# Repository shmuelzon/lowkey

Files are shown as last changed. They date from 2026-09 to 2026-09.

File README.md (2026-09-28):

# LowKey

A battery-powered smart lock controller for a motorised deadbolt, built on the
Nordic **nRF54L15** with the nRF Connect SDK.

It speaks **Matter over Thread** and a **custom BLE GATT service at the same
time**, on one Bluetooth controller. The two are not alternatives selected at
build time - they run concurrently, each with its own advertising set and its
own Bluetooth identity, so the lock stays controllable over BLE when the Thread
mesh or the Matter controller is down, and its BLE bonds survive Matter
commissioning and Matter factory resets.

| On the bench | Installed in a door |
| --- | --- |
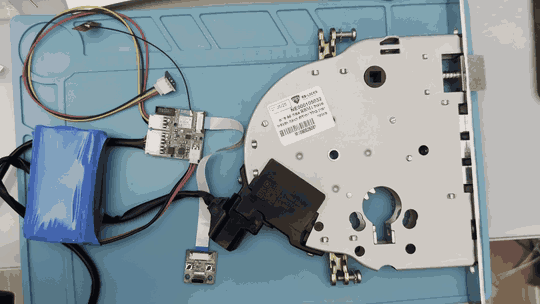
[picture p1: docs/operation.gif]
Locking and unlocking the RBM1 lock body, with the unassembled controller and UI boards on the bench
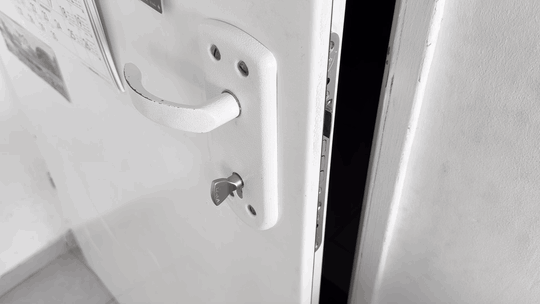
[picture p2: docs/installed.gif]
The installed lock throwing and retracting its bolts from the edge of a door
|  |  |

## Features

- **Three distinct actions**, matching what a mortise deadbolt can actually do:
  lock, unbolt (retract the bolt, spring latch still holds the door), and open
  (retract the bolt *and* hold the latch back so the door can be pushed).
  These map to the Matter `LockDoor`, `UnboltDoor` and `UnlockDoor` commands.
- **Position tracked from the bolt, not from the motor.** The lock body's two
  magnetic end-stop sensors are monitored continuously, so operating the lock
  with a physical key updates the reported state exactly like a remote command
  does.
- **Jam detection** - the motor stops and the lock reports jammed, with a Matter
  `DoorLockAlarm` event, if an end-stop is not reached in time.
- **Door position sensor**, reported as a Matter `DoorStateChange`.
- **Battery monitoring** with a MAX17205 ModelGauge m5 fuel gauge, plus charger
  connected/complete status.
- **Firmware update** over both Bluetooth SMP (MCUmgr) and Matter OTA, sharing
  one MCUboot slot pair with LZMA-compressed images.
- **Per-device provisioning** - serial number, BLE pairing passkey, Matter
  discriminator and SPAKE2+ verifier in a dedicated flash partition that OTA
  never touches.
- **Task watchdog** with a channel per critical thread.

## Hardware

### Lock body

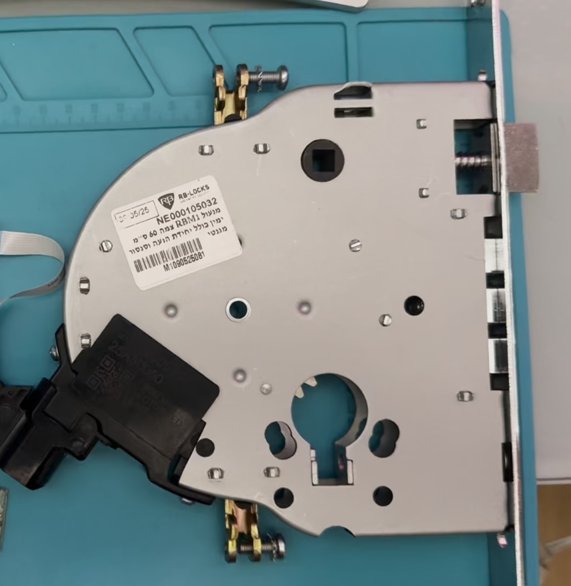
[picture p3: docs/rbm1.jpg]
The RBM1 lock body, with its motor unit at the lower left


The mechanism is a **Rav Bariach RBM1**, a motorised mortise lock. The motor
unit and the magnetic sensors for the two bolt end-stops come built into the
body. The controller only has to drive the motor and read the sensors, all
through one 6-pin harness:

| Pin | Signal |
| --- | --- |
| 1 | 3.3 V (sensor supply) |
| 2 | GND |
| 3 | Unlocked end-stop |
| 4 | Locked end-stop |
| 5, 6 | Motor |

See [Adapting to a different lock body](#adapting-to-a-different-lock-body) if
yours is different.

<br clear="right">

### Electronics

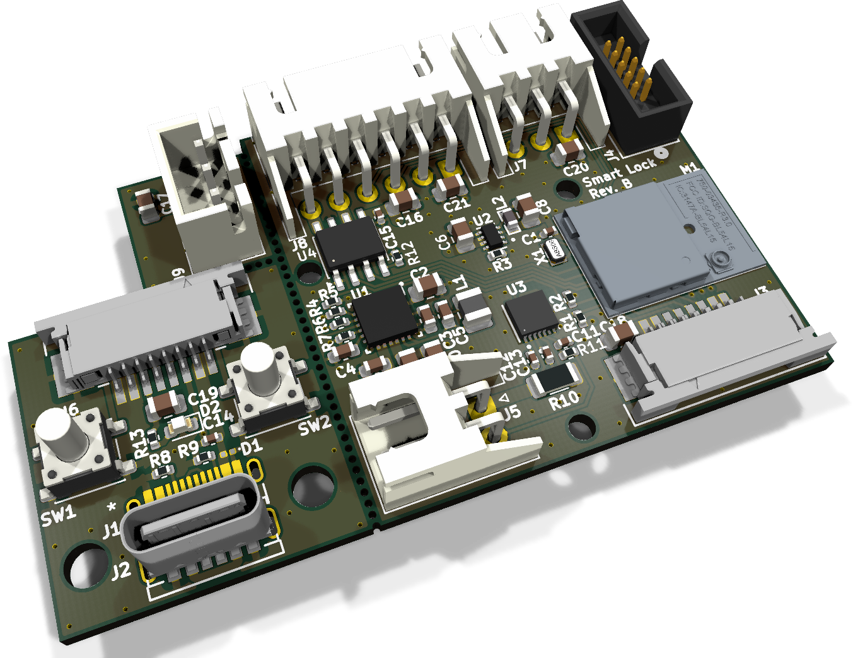
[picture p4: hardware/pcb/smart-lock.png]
3D render of the PCB panel


One KiCad project holds three boards, panelised with mouse bites:

- **Main board**: the **Ezurio BL54L15** module (nRF54L15, with an MHF4
  connector for an external antenna, so there is no RF switch to manage),
  charger, regulator, fuel gauge, motor driver, and connectors for the
  battery, the lock harness, the door sensor and SWD.
- **UI board**: the two keys, the status LED and the USB-C charging port. It
  connects to the main board over an 8-way FFC.
- **Door sensor board**: a single Hall sensor with a 3-pin JST XH cable to
  the main board. It also carries an alternative footprint for a Coto RR123
  magnetoresistive sensor, which is not fitted.

Power comes from a 2S Li-ion pack, two 18650 or 21700 cells in series, on a
2-pin JST XH connector. See [Battery life](#battery-life) for what to expect
from each.

| Part | Role |
| --- | --- |
| Ezurio 453-00044R (BL54L15) | nRF54L15 module |
| TE 2344656-6 | External 2.4 GHz antenna |
| TI BQ25886 | 2S battery charger from USB-C, 1.03 A charge current (ITERM 103 mA) |
| TI TPS629203 | 3.3 V buck regulator |
| ADI MAX17205 | 2S fuel gauge, I²C `0x36`, 10 mΩ shunt |
| TI DRV8871 | H-bridge motor driver |
| Honeywell SL353LT | Door sensor, on its own board |

- [**Schematic (PDF)**](hardware/pcb/smart-lock.pdf)
- [KiCad project](hardware/pcb/) (KiCad 10). Custom 3D models are embedded
  in the board file, so the 3D viewer needs no extra libraries.

### Enclosures

| Controller | UI |
| --- | --- |
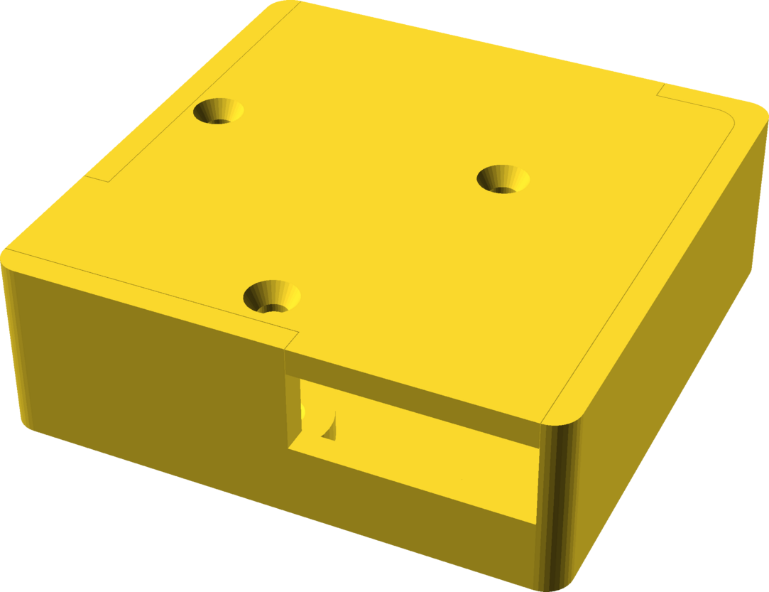
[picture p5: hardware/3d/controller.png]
Controller enclosure
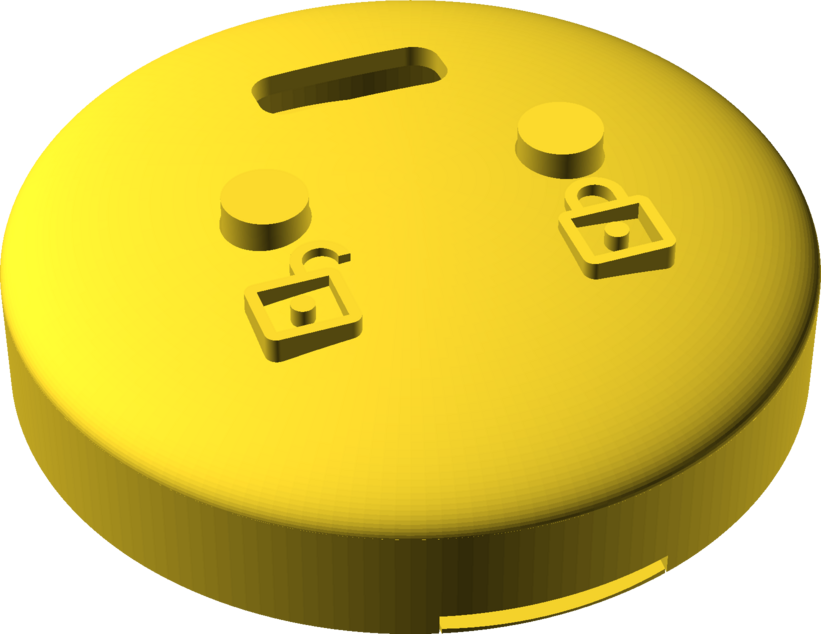
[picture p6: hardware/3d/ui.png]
UI enclosure
|  |  |
| [`controller.stl`](hardware/3d/controller.stl), from [`controller.scad`](hardware/3d/controller.scad) | [`ui.stl`](hardware/3d/ui.stl), from [`ui.scad`](hardware/3d/ui.scad) |

- **Controller**: a 42 × 42 × 13.8 mm box for the main board. It has openings
  for the lock harness, the battery lead and the UI cable, and closes with
  three M2 countersunk screws into heat-set inserts.
- **UI**: a Ø34 mm dome for the UI board, with lock and unlock icons embossed
  beside the two key caps. It closes with two M2 countersunk screws into
  heat-set inserts.

Both enclosures use 3.45 mm outer-diameter M2 inserts. Each STL holds every
part of its enclosure (base, lid and, for the UI, the key caps) as separate
bodies; split them into objects in your slicer. The `show_*` variables at the
top of each `.scad` export a single part.

### Regenerating the outputs

The PDF, the renders and the STLs are committed so they can be viewed on
GitHub. After changing a source, regenerate them with:

```sh
make -C hardware          # everything
make -C hardware pcb      # schematic PDF and board render (KiCad 10)
make -C hardware 3d       # STLs and enclosure renders (OpenSCAD)
```

The Makefile finds `kicad-cli`, `openscad` and ImageMagick's `magick` in
`PATH`, in their usual macOS locations, and under `C:\Program Files` from WSL or
Git Bash. Point it at a tool anywhere else with
`make KICAD_CLI=... OPENSCAD=... MAGICK=...`. ImageMagick is optional: it gives
the renders a transparent background and trims them to the model.

OpenSCAD must be a development snapshot with the Manifold backend. The 2021.01
release only has CGAL, which rejects the imported PCB meshes and silently drops
their cutouts, so the Makefile refuses to use it.

## Repository layout

```
boards/shmuelzon/lowkey/   Board definition (revisions A and B) and its DTS bindings
src/                       Application
  ├─ lock_manager.c        Motor drive and the bolt/latch state machine
  ├─ door_monitor.c        Door position sensor
  ├─ battery_manager.c     MAX17205 fuel gauge and charger status
  ├─ ui.c                  Keys and status LED
  ├─ gpio_input.c          Interrupt-driven GPIO inputs, optionally debounced
  ├─ watchdog.c            Task watchdog
  ├─ radio.c               Fans the radio API out to the backends below
  ├─ ble/                  Custom GATT services (CONFIG_LOCK_RADIO_BLE)
  └─ matter/               Clusters and ZAP data model (CONFIG_LOCK_RADIO_MATTER)
scripts/                   Factory-data generation, device label, Intel HEX padding
sysbuild/mcuboot/          MCUboot configuration
pm_static.yml              Flash partition layout
hardware/                  Makefile that regenerates the outputs below
  ├─ pcb/                  KiCad project, schematic PDF and board render
  └─ 3d/                   OpenSCAD enclosures, STLs and renders
docs/                      README media
```

## Getting started

Built against **nRF Connect SDK v3.2.4**.

```sh
# Toolchain and SDK
curl -o ~/bin/nrfutil "https://files.nordicsemi.com/ui/api/v1/download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"
chmod +x ~/bin/nrfutil
nrfutil install sdk-manager toolchain-manager
nrfutil sdk-manager install v3.2.4
cd ~/ncs/v3.2.4 && west update

# Per-shell environment (needed for west build and west zap-generate)
SDK_VERSION=v3.2.4
source ~/ncs/$SDK_VERSION/zephyr/zephyr-env.sh
eval $(nrfutil toolchain-manager env --ncs-version $SDK_VERSION --as-script)

# Python packages used by the provisioning script
pip install cbor2 intelhex jsonschema pillow pyyaml qrcode
```

## Building

The board has two PCB revisions, selected with the `@` suffix. They differ only
in the motor driver: **rev A** (DRV8837) has an `nSLEEP` enable pin, **rev B**
(DRV8871) sleeps on its own and omits it.

```sh
# Product build: both radios, release
west build --pristine -b lowkey@B/nrf54l15/cpuapp -- -DBOARD_ROOT="$PWD"

# Debug: RTT console and logging
west build --pristine -b lowkey@B/nrf54l15/cpuapp -- -DBOARD_ROOT="$PWD" \
    -DEXTRA_CONF_FILE="overlay-debug.conf"

# One radio only
west build --pristine -b lowkey@B/nrf54l15/cpuapp -d build-ble -- \
    -DBOARD_ROOT="$PWD" -DCONFIG_LOCK_RADIO_MATTER=n -DSB_CONFIG_MATTER=n
west build --pristine -b lowkey@B/nrf54l15/cpuapp -d build-matter -- \
    -DBOARD_ROOT="$PWD" -DCONFIG_LOCK_RADIO_BLE=n
```

Both radios are on by default. There are no `prj_*.conf` protocol fragments -
`CONFIG_LOCK_RADIO_BLE` and `CONFIG_LOCK_RADIO_MATTER` in the project `Kconfig`
carry all protocol-specific configuration, so a build is described by the board
plus those two switches.

Approximate image sizes (of the 810 KiB application slot):

| Build | Flash | RAM |
| --- | --- | --- |
| Both radios | 78 % | 79 % |
| Both radios, debug | 90 % | 80 % |
| Matter only | 72 % | 68 % |
| BLE only | 24 % | 28 % |

Two things that will bite you:

- **Use `-DEXTRA_CONF_FILE`, not `-DOVERLAY_CONFIG`.** Under sysbuild the latter
  is applied to *every* image, including MCUboot, where it breaks image signing
  with a confusing `@PM_MCUBOOT_PRIMARY_SIZE@ is not a valid integer`.
- **`-DSB_CONFIG_MATTER=n` is separate from `-DCONFIG_LOCK_RADIO_MATTER=n`.**
  Sysbuild's Kconfig cannot see the application's, so a Matter-less build still
  emits a `matter.ota` artifact unless you pass both.

### Changing the Matter data model

The files under `src/matter/zap-generated/` are generated from
`src/matter/lock.zap`:

```sh
west zap-gui        # or edit the JSON directly
west zap-generate
```

If you **add or remove a cluster**, force a CMake reconfigure before rebuilding
(`touch CMakeLists.txt`, or build `--pristine`). Cluster-to-source selection
happens at configure time only, so an incremental build fails at link with
something like `undefined reference to MatterPowerSourcePluginServerInitCallback`.

## Flashing

A build produces `build/merged.hex` (MCUboot + signed application) for SWD,
`build/dfu_application.zip` for MCUmgr, and `build/matter.ota` for Matter OTA.

```sh
./scripts/pad_hex.py build/merged.hex
west flash
```

> ### Pad the HEX file first
>
> `scripts/pad_hex.py` pads the last data record of an Intel HEX file to 16
> bytes with `0xFF`. This works around an OpenOCD nRF5 driver issue where the
> RRAMC write buffer is not flushed for a trailing partial block, which
> **silently corrupts the ED25519 signature** at the end of the MCUboot image -
> the device then refuses to boot for no visible reason.
>
> This affects on-board debuggers driven through OpenOCD, including the one on
> the Seeed XIAO nRF54L15. Run it before every flash, on `merged.hex` and on
> `factory_data.hex` alike. It is idempotent.

## Provisioning

Every device needs its own factory data: a serial number, a BLE pairing
passkey, and (for Matter) a discriminator and SPAKE2+ verifier. These live in a
4 KiB `factory_data` partition that firmware updates never overwrite.

```sh
python3 scripts/generate_factory_data.py -o factory_data
./scripts/pad_hex.py factory_data.hex
nrfutil device program --firmware factory_data.hex --core application \
    --options chip_erase_mode=ERASE_RANGES_TOUCHED_BY_FIRMWARE,reset=RESET_SYSTEM
```

Every argument has a default and the per-device secrets are drawn randomly when
not given, so the command above is the whole flow for a development unit. It
writes five files:

| File | Contents |
| --- | --- |
| `factory_data.hex` | The partition image, at the offset and size read from `pm_static.yml` |
| `factory_data.json` | Every generated value **except** the Matter passcode |
| `factory_data.txt` | Matter manual pairing code and QR payload |
| `factory_data.png` | The same QR code as an image |
| `factory_data.sticker.png` | A printable device label: Matter QR and pairing code, BLE name, serial number and BLE passkey |

Archive the `.json` and `.txt` per device - together they are the only record.
Use `--no-matter` for a BLE-only build, and `--help` for the full set of
overrides (`--sn`, `--ble_passkey`, `--passcode`, `--discriminator`,
`--battery_capacity_mah`, the DAC/PAI certificate paths, `--sticker-size`,
`--no-sticker`, …). To reprint the label for a unit provisioned earlier, run
`python3 scripts/generate_sticker.py factory_data`.

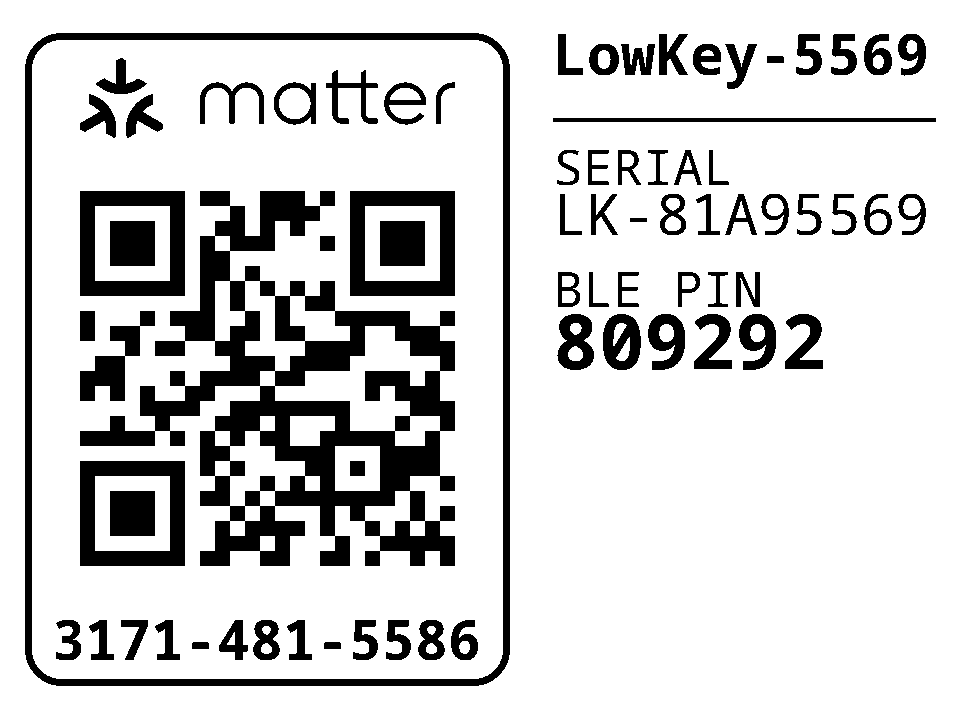
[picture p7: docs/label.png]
Example device label: Matter QR code and manual pairing code beside the BLE name, serial number and BLE PIN


*An example label. Its codes were randomly generated and belong to no device.*

> ### The onboarding codes printed at boot are wrong
>
> The Matter passcode is deliberately **not** stored on the device - only the
> one-way SPAKE2+ verifier is, so reading out the flash does not reveal it. The
> firmware therefore cannot rebuild its own onboarding payload and falls back to
> Matter's example passcode, making the `Manual pairing code` and `SetupQRCode`
> lines in its boot log useless:
>
> ```
> [DL]  Setup Pin Code (0 for UNKNOWN/ERROR): 0
> [SVR]*** Using default EXAMPLE passcode 20202021 ***
> ```
>
> **Commission with the codes in `factory_data.txt`.** Pass `--include-passcode`
> if you would rather store the passcode and trust the boot log, at the cost of
> it being readable out of flash.

### Before shipping anything

The stock configuration is a development configuration:

- **Attestation certificates** default to the Matter SDK's *test* DAC/PAI for
  test VID/PID `0xFFF1`/`0x8000`. Production devices need certificates from a
  real PAA. The script warns if you change the VID/PID without supplying them.
- **Images are signed with MCUboot's public development key**, so anyone can
  produce an image this bootloader accepts. Generate your own and point the
  build at it - this cannot be changed after units ship, because MCUboot is the
  immutable first-stage bootloader:
  ```sh
  imgtool keygen -k prod-ed25519.pem -t ed25519
  west build ... -- -DSB_CONFIG_BOOT_SIGNATURE_KEY_FILE="$PWD/prod-ed25519.pem"
  ```
  On nRF54L15, `SB_CONFIG_BOOT_SIGNATURE_USING_KMU` can hold the public key in
  hardware instead of bootloader flash.

## Using the lock

### Keys and LED

The key layout is chosen at build time from devicetree, by whether a `key1`
alias exists:

| | Short press | Long press |
| --- | --- | --- |
| **key0** | Lock | Factory reset (10 s) |
| **key1** | Unbolt | Open for commissioning / pairing (1.5 s) |

On a board with only `key0`, a short press opens the discovery window and the
long press is still factory reset - both are mandatory in every layout, and the
build fails if either is unassigned. Factory reset sits on the *lock* key
deliberately: the key someone leans on when the door will not open is the unlock
one, and ten seconds of that should not wipe the fabric.

| LED | Meaning |
| --- | --- |
| Fast blink (100 ms) | Factory reset fires in 3 seconds - release to abort |
| Slow blink (500 ms) | Discoverable, identifying, or charging |
| Solid | Charge complete |
| Off | Idle |

One press of the discovery key opens an onboarding window on **both** radios and
lets your app pick; the first to complete closes the other. To pair a BLE client
*and* commission to Matter, press it twice, once per path.

### Matter

Endpoint 1 exposes **Door Lock** (with the `Unbolting` and `DoorPositionSensor`
features), **Power Source**, **Identify** and **ICD Management**. There is no
PIN/RFID/user support - the lock has no keypad, and those cluster features are
deliberately absent from the data model rather than stubbed.

The device is a Thread **sleepy end device**. Inbound latency is bounded by the
ICD poll interval (500 ms idle); outbound reporting of bolt and door changes is
immediate.

### BLE

| Service / characteristic | UUID | Properties |
| --- | --- | --- |
| Lock service | `1e3557d1-0001-5887-a357-c9acbd789b14` | |
| ├ Lock status | `1e3557d1-0002-5887-a357-c9acbd789b14` | Read, Notify (encrypted) |
| └ Lock request | `1e3557d1-0003-5887-a357-c9acbd789b14` | Write (authenticated) |
| Door service | `1e3557d1-0010-5887-a357-c9acbd789b14` | |
| └ Door state | `1e3557d1-0011-5887-a357-c9acbd789b14` | Read, Notify (encrypted) |
| Battery service | `0x180F` | Standard |
| Device Information | `0x180A` | Populated from factory data |

Lock status values: `0` locked, `1` locking, `2` unlocked, `3` unlocking,
`4` jammed, `5` unlatched, `6` unknown. Lock request values: `0` lock,
`1` unbolt, `2` open.

The lock advertises as `LowKey-XXXX`, where `XXXX` is the last four characters
of the serial number, so the name on the label matches without reading anything
off the device.

## Porting to another board

The application depends only on the devicetree contract below - no board-specific
code. Everything is reached through aliases except three node labels.

### Required aliases

| Alias | Direction | Expected wiring |
| --- | --- | --- |
| `led0` | Output | Status LED |
| `key0` | Input | Push button, active low with pull-up |
| `key1` | Input | Second button. **Optional** - its presence changes the key layout |
| `lock-sensor` | Input | Active when the bolt is fully extended |
| `unlock-sensor` | Input | Active when the bolt is fully retracted |
| `door-sensor` | Input | Active when the door is closed |
| `chg-power-good` | Input | Active when input power is present |
| `chg-stat` | Input | Active while charging; inactive means complete |

Every input is configured for **both-edge interrupts**, so all of them must be
on interrupt-capable pins. On the nRF54L15 that means P0 or P1 - **P2 has no
GPIOTE peripheral**.

### Required node labels

| Label | Notes |
| --- | --- |
| `motor_driver` | `compatible = "lowkey,motor-driver"`; `in1-gpios` and `in2-gpios` required, `nsleep-gpios` optional |
| `max17205` | `compatible = "maxim,max17205"`, `reg = <0x36>`, `sense-resistor-micro-ohms`, `charge-term-current-microamp` |
| `wdt31` | Referenced by label, not by the `watchdog0` alias, and must be `status = "okay"` |

Plus a `factory_data` partition, supplied by Partition Manager from
`pm_static.yml`.

### Board-level requirements

- **`&cpuapp_rram { reg = <0x0 DT_SIZE_K(1524)>; }` in every image**, including
  MCUboot (`sysbuild/mcuboot/app.overlay`). `pm_static.yml` spans the full
  1524 KiB by reclaiming the unused FLPR coprocessor's RRAM; miss this in any
  one image and the layout overflows `flash_primary` and the build fails.
- **`&uicr { nfct-pins-as-gpios; }`** if you reuse P1.02/P1.03. These power up in
  NFC mode, and the NFCT pad network holds them low, overriding the GPIO
  pull-ups - the keys read stuck-low. Disabling the `nfct` node is *not* enough.
- **Disable `uart21` in MCUboot** on any board that enables it. If the UARTE
  driver initialises during MCUboot, its pins latch as UART-TX-idle-high and
  that hardware state survives into the application, overriding GPIO output.
- Keep application RAM low if you care about idle current: `power_down_unused_ram()`
  powers down whole 32 KiB SRAM sections above the image, so every 32 KiB the
  image gives back is one more section switched off.

### Tunables

All in the project `Kconfig`, prefixed `CONFIG_LOCK_`:

| Symbol | Default | Purpose |
| --- | --- | --- |
| `MOTOR_TIMEOUT_MS` | 3000 | End-stop not reached in this time ⇒ jammed |
| `MOTOR_BRAKE_US` | 2000 | Dynamic braking before coasting and before reversing |
| `BOLT_SEATING_MS` | 100 | Extra drive after the lock end-stop, to seat the bolt |
| `UNBOLT_SEATING_MS` | 0 | Extra drive after the unlock end-stop |
| `LATCH_RELEASE_MS` | 500 | Extra drive on an open, to hold the latch back |
| `BATTERY_POLL_INTERVAL_S` | 60 | Fuel gauge polling |
| `BUTTON_DEBOUNCE_MS` | 30 | Mechanical key debounce |
| `WATCHDOG_TIMEOUT_MS` | 30000 | Task watchdog, per channel |
| `WATCHDOG_FEED_MS` | 5000 | Feed interval |
| `DISCOVERY_TIMEOUT_S` | 180 / 60 | Onboarding window (180 with Matter) |
| `DISCOVERY_PRESS_MS` | 1500 | Hold time for discovery |
| `FACTORY_RESET_PRESS_MS` | 10000 | Hold time for factory reset |
| `BLE_TX_POWER_DBM` | 7 | Applied at runtime over vendor HCI |

## Adapting to a different lock body

The mechanism needs, at minimum:

- **Two motor pins** into an H-bridge (`in1-gpios`, `in2-gpios`), plus an
  optional enable pin (`nsleep-gpios`) if the driver has one.
- **Two end-stop sensors** telling the firmware when the bolt has reached each
  extreme.
- **One door sensor** (optional in practice - omit the Matter
  `DoorPositionSensor` feature from `lock.zap` if you have none).

The H-bridge is driven as:

| IN1 | IN2 | Effect |
| --- | --- | --- |
| 0 | 0 | Coast (idle) |
| 0 | 1 | Drive toward locked |
| 1 | 0 | Drive toward unlocked |
| 1 | 1 | Brake |

Swap `in1-gpios` and `in2-gpios` if your motor runs the wrong way.

Sensors are expected to be **solid-state, active-low, with no pull-up** - Hall
sensors with a push-pull output stage, where a pull-up would only waste current.
They are deliberately **not debounced**: they do not bounce, and any delay here
lands between the end-stop firing and the motor stopping, adding bolt travel.
Only the mechanical keys are debounced. If you use reed switches or another
bouncing sensor, pass a non-zero debounce to `gpio_input_init()` in
`lock_manager.c` and `door_monitor.c`.

Timing notes for a different mechanism:

- `LATCH_RELEASE_MS` **is** the window during which the door can be pushed open.
  The latch is spring-loaded and returns the instant the motor releases the cam,
  so this is a usability number, not just a mechanical one.
- `UNBOLT_SEATING_MS` defaults to 0 because on this lock the unbolt travel heads
  *toward* the latch, so any extra drive starts releasing it. If your mechanism
  is different, this is where extra retraction goes.
- A Matter build **refuses** `LATCH_RELEASE_MS=0` (a `BUILD_ASSERT`), because
  `lock.zap` advertises the Door Lock `Unbolting` feature, which promises a
  controller that `UnlockDoor` pulls the latch. Clear that feature bit from the
  FeatureMap if your lock cannot.

## Power

The design targets a multi-year battery life on a 2S pack. What the firmware
does for it:

- `vregmain` in DCDC mode, and unused SRAM sections powered down at boot.
- Thread MTD/sleepy end device, with the ICD intervals retuned - the NCS
  defaults are self-defeating, because the fast poll interval is longer than the
  active-mode duration, so the fast interval is unreachable and every round trip
  of a multi-message exchange pays the full idle interval.
- BLE advertising slows to a ~1 s interval once bonded.
- The motor driver sleeps between operations, and the fuel gauge is polled once
  a minute plus once after each completed operation.
- Runtime device PM, so the I²C peripheral is suspended between transfers.

### Battery life

Measured draw:

| State | Current |
| --- | --- |
| Idle | 70 µA |
| Motor running | 200 mA, for about 1 s per lock or unlock |

At around 40 lock/unlock cycles a day, a pack of two 3000 mAh 18650 cells in
series is expected to last about 1.3 years, and two 5000 mAh 21700 cells about
2.2 years.

## Known limitations

- **The onboarding codes in the boot log are wrong** unless you provision with
  `--include-passcode`. See
  [above](#the-onboarding-codes-printed-at-boot-are-wrong).
- **Partition boundaries are permanent.** MCUboot is the immutable first-stage
  bootloader with the slot offsets compiled into it, there is no NSIB `s0`/`s1`
  pair, and serial recovery is off - it could not work anyway, since the board
  enables no UART. Changing any address in `pm_static.yml` means reflashing over
  SWD.
- **MCUboot is not write-protected at runtime.** `fprotect` caps a protected
  region at 62 KiB and the bootloader partition is 72 KiB, so enabling it would
  make MCUboot halt at startup. Shrinking the partition below 62 KiB is the only
  way to have both.
- **The Matter module is required even for a BLE-only build.** The application
  reads factory data with the SDK's `FactoryDataParser.c`, which lives in the
  Matter module; it depends only on zcbor, so it links without the rest of the
  stack, but the module has to be present.
- **The watchdog does not cover the Bluetooth RX thread.** It has a channel for
  the system workqueue and one for the Matter event loop.

## License

MIT - see [LICENSE](LICENSE).

Files under `boards/shmuelzon/lowkey/` derive from nRF Connect SDK board
templates and remain Apache-2.0, as marked in their headers.

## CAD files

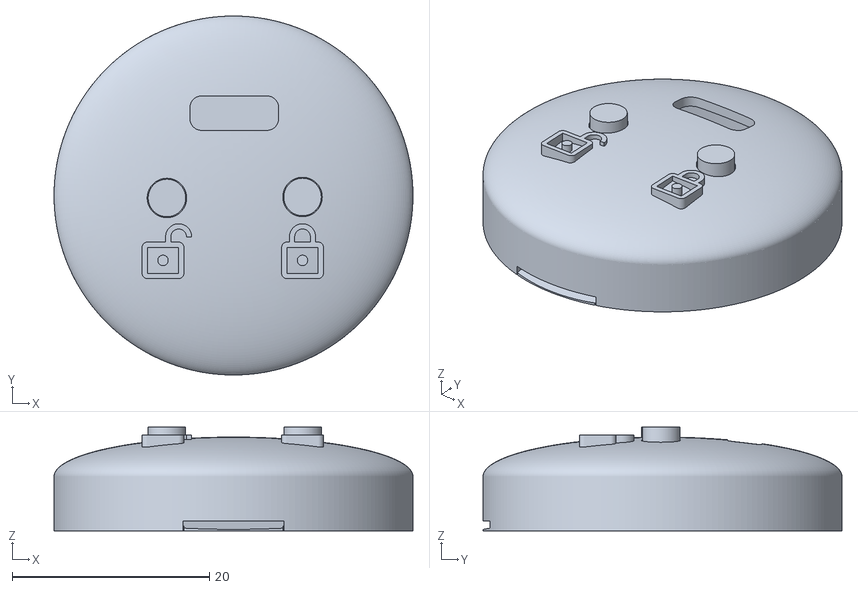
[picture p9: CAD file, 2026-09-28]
hardware/3d/ui.stl
36.4 x 36.4 x 10.5

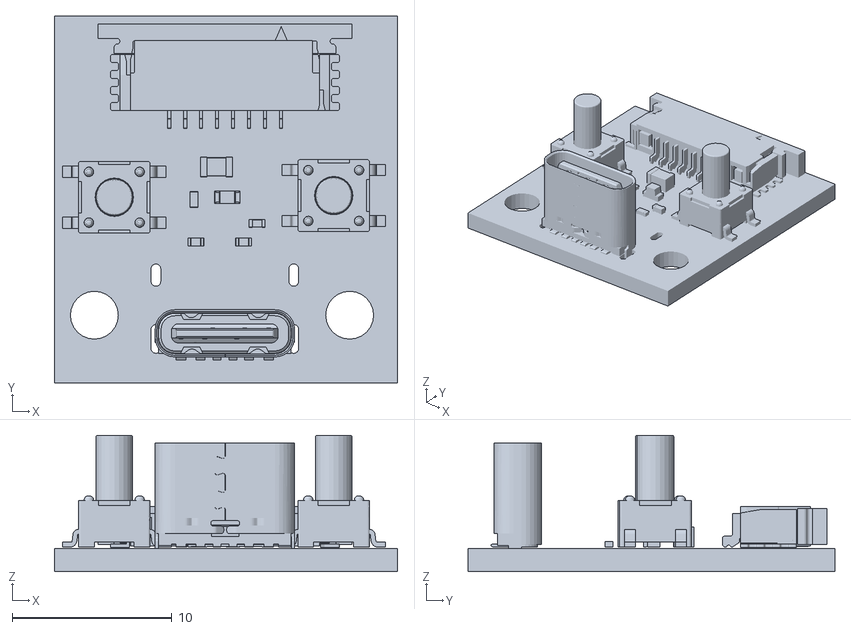
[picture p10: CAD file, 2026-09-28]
hardware/3d/ui_pcb.stl
21.5 x 23.0 x 8.55

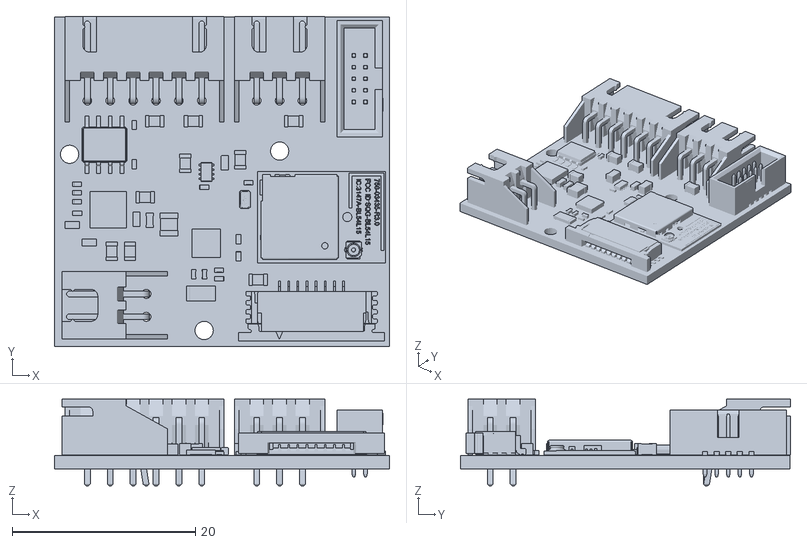
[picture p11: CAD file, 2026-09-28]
hardware/3d/controller_pcb.stl
36.6 x 36.1 x 9.50

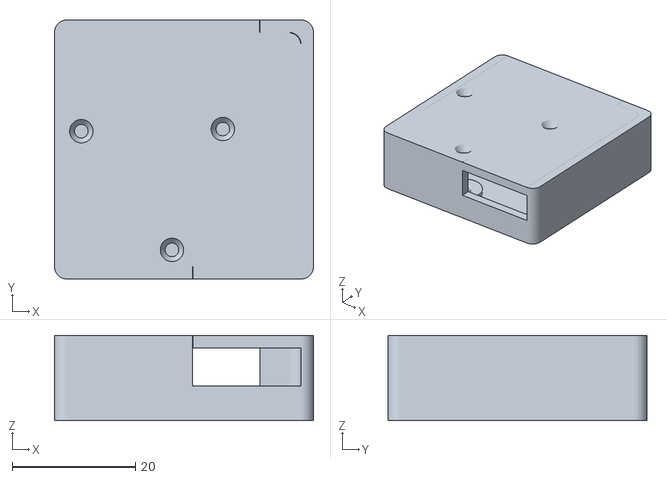
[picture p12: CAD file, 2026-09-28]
hardware/3d/controller.stl
42.0 x 42.0 x 13.8

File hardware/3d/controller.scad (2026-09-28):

show_bottom = true;
show_top = true;
$fn = 36;

EPSILON = 0.01;
MECHANICAL_CLEARANCE = 0.1;

WALL_THICKNESS = 2;

CASE_WIDTH = 42;
CASE_DEPTH = 42;
CASE_HEIGHT = 13.8;

COVER_SIZE = [CASE_WIDTH - (WALL_THICKNESS * 2) - MECHANICAL_CLEARANCE, CASE_DEPTH - (WALL_THICKNESS * 2) - MECHANICAL_CLEARANCE, WALL_THICKNESS];

LOCK_OPENING = [27.2, WALL_THICKNESS];
BATTERY_OPENING = [WALL_THICKNESS, 6];
UI_OPENING = [13.5, WALL_THICKNESS];
PCB_AND_THROUGH_HOLE_HEIGHT = 3.6;

SCREW_LOCATIONS = [
  [6.3, 3.32],
  [-16.65, 2.97],
  [-1.95, -16.28],
];

module centered_cube(size=[0, 0, 0])
{
  translate([-size[0] / 2, -size[1] / 2, 0]) cube(size);
}

module round_cube(size, r)
{
  minkowski()
  { 
    centered_cube([size[0] - (2 * r), size[1] - (2 * r), size[2] - 0.01]);
    cylinder(r=r, h=0.01);
  }
}

module round_shell(size, wall_thickness1, r, wall_thickness2 = 0, r_inner = 0)
{
  difference()
  {
    round_cube(size, r);
    translate([0, 0, -EPSILON]) round_cube([size[0] - (wall_thickness1 * 2), size[1] - ((wall_thickness2 != 0 ? wall_thickness2 : wall_thickness1) * 2), size[2] + (2 * EPSILON)], (r_inner != 0 ? r_inner : r));
  }
}

module m2_countersunk_screw(length)
{
  color("gray")
  {
    cylinder(h=length, r=1 + MECHANICAL_CLEARANCE);
    translate([0, 0, length]) cylinder(h=1.4, r1=1 + MECHANICAL_CLEARANCE, r2=1.8 + MECHANICAL_CLEARANCE);
  }
}

module m2_insert()
{
  INSERT_DIAMETER=3.45;
  INSERT_HEIGHT=3;

  color("gold");
  {
    cylinder(h=INSERT_HEIGHT - 0.5, r=(INSERT_DIAMETER * 0.9 ) / 2);
    translate([0, 0, INSERT_HEIGHT - 0.5]) cylinder(h=0.5, r1=(INSERT_DIAMETER * 0.9 ) / 2, r2=(INSERT_DIAMETER / 2) + 0.2);
  }

}

module pcb() {
  translate([0, 0, 7]) color("gray", 0.5) import("controller_pcb.stl", center=true);
}

module case_bottom()
{
  difference()
  {
    round_cube([CASE_WIDTH, CASE_DEPTH, CASE_HEIGHT], 2);
    translate([0, 0, WALL_THICKNESS]) round_cube([CASE_WIDTH - (WALL_THICKNESS * 2), CASE_DEPTH - (WALL_THICKNESS * 2), CASE_HEIGHT - WALL_THICKNESS + EPSILON], 2);
    cutouts();
  }

  // Screw inserts housing
  for (screw_location = SCREW_LOCATIONS)
    translate([screw_location[0], screw_location[1], WALL_THICKNESS]) cylinder(r=4, h=2);
}

module case_top()
{
  translate([0, 0, CASE_HEIGHT - WALL_THICKNESS]) round_cube(COVER_SIZE, 2);

  // cutout covers
  translate([0, 0, CASE_HEIGHT - WALL_THICKNESS])
  {
    translate([-COVER_SIZE[0] / 2, COVER_SIZE[1] / 2 - (WALL_THICKNESS * 2) + 0.05, 0]) cube([LOCK_OPENING[0] + WALL_THICKNESS * 2, LOCK_OPENING[1] + WALL_THICKNESS * 2, WALL_THICKNESS]);
    translate([-COVER_SIZE[0]  / 2 - WALL_THICKNESS - 0.05, -COVER_SIZE[1] / 2, 0]) cube([BATTERY_OPENING[0] + (WALL_THICKNESS * 2), BATTERY_OPENING[1] + WALL_THICKNESS * 2, WALL_THICKNESS]);
    translate([(COVER_SIZE[0] / 2) - UI_OPENING[0] - WALL_THICKNESS * 2, -(COVER_SIZE[1] / 2 - UI_OPENING[1]) - WALL_THICKNESS * 2 - 0.05, 0]) cube([UI_OPENING[0] + WALL_THICKNESS * 2, UI_OPENING[1] + (WALL_THICKNESS * 2), WALL_THICKNESS]);
  }
}

module cutouts()
{
  translate([0, 0, WALL_THICKNESS + PCB_AND_THROUGH_HOLE_HEIGHT])
  {
    translate([-COVER_SIZE[0] / 2 - 0.05, COVER_SIZE[1] / 2 - WALL_THICKNESS + 0.05, 0]) cube([LOCK_OPENING[0] + WALL_THICKNESS * 2 + 0.05 * 2, LOCK_OPENING[1] + WALL_THICKNESS, CASE_HEIGHT - PCB_AND_THROUGH_HOLE_HEIGHT - WALL_THICKNESS]);
    translate([-COVER_SIZE[0]  / 2 - WALL_THICKNESS - 0.05, -COVER_SIZE[1] / 2 - 0.05, 0]) cube([BATTERY_OPENING[0] + WALL_THICKNESS, BATTERY_OPENING[1] + WALL_THICKNESS * 2 + 0.05 * 2, CASE_HEIGHT - PCB_AND_THROUGH_HOLE_HEIGHT - WALL_THICKNESS]);
    translate([(COVER_SIZE[0] / 2) - UI_OPENING[0] - WALL_THICKNESS * 2 - 0.05, -(COVER_SIZE[1] / 2 - UI_OPENING[1]) - WALL_THICKNESS * 2 - 0.05, 0]) cube([UI_OPENING[0] + WALL_THICKNESS * 2 + 0.05 * 2, UI_OPENING[1] + WALL_THICKNESS, CASE_HEIGHT - PCB_AND_THROUGH_HOLE_HEIGHT - WALL_THICKNESS]);
  }
}

module hardware()
{
  SCREW_HEIGHT = 10.8;
  for (screw_location = SCREW_LOCATIONS)
  {
    translate([screw_location[0], screw_location[1], WALL_THICKNESS - 0.4]) m2_countersunk_screw(SCREW_HEIGHT);
    translate([screw_location[0], screw_location[1], 1]) m2_insert();
  }
}

difference()
{
  union()
  {
    if (show_bottom) case_bottom();
    if (show_top) case_top();
  }
  pcb();
  hardware();
}

if ($preview)
{
  pcb();
  hardware();
}

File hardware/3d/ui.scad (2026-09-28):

show_bottom = true;
show_top = true;
show_buttons = true;
$fn = 180;

EPSILON = 0.01;
MECHANICAL_CLEARANCE = 0.1;

WALL_THICKNESS = 1.2;

CASE_DIAMETER = 34;
CASE_HEIGHT = 5.5;
DOME_HEIGHT = 4;

SCREW_LOCATIONS = [
  [8.25, 7.25],
  [-7.75, 7.25],
];

BUTTONS_LOCATIONS = [
  [7, -0.15],
  [-6.75, -0.25],
];

module m2_countersunk_screw(length)
{
  color("gray")
  {
    cylinder(h=1.4, r1=1.8 + MECHANICAL_CLEARANCE, r2=1 + MECHANICAL_CLEARANCE);
    translate([0, 0, 1.4])cylinder(h=length, r=1 + MECHANICAL_CLEARANCE);
  }
}

module m2_insert()
{
  INSERT_DIAMETER=3.45;
  INSERT_HEIGHT=5;

  color("red")
  {
    cylinder(h=0.5, r1=(INSERT_DIAMETER / 2) + 0.2, r2=(INSERT_DIAMETER * 0.9 ) / 2);
    translate([0, 0, 0.5]) cylinder(h=INSERT_HEIGHT - 0.5, r=(INSERT_DIAMETER * 0.9 ) / 2);
  }

}

module centered_cube(size=[0, 0, 0])
{
  translate([-size[0] / 2, -size[1] / 2, 0]) cube(size);
}

module round_cube(size, r)
{
  minkowski()
  { 
    centered_cube([size[0] - (2 * r), size[1] - (2 * r), size[2] - 0.01]);
    cylinder(r=r, h=0.01);
  }
}

module dome(r, h)
{
  difference()
  {
    intersection()
    {
      scale([1, 1, h / r]) sphere(r = r);
      translate([-r, -r, 0]) cube([r * 2, r * 2, h]);
    } 
    intersection()
    {
      scale([1, 1, (h - WALL_THICKNESS) / (r - WALL_THICKNESS)]) sphere(r=r - WALL_THICKNESS);
      translate([-r, -r, -0.01]) cube([r * 2, r * 2, h]);
    }
  }
}

module pcb() {
  translate([0, 0, 4.28 + WALL_THICKNESS])
  color("green", 1)
  rotate([0, 0, 180])
  import("ui_pcb.stl", center=true);
}

module case_bottom() {
  difference()
  {
    union()
    {
      cylinder(r=CASE_DIAMETER / 2 - MECHANICAL_CLEARANCE, h=WALL_THICKNESS);
      intersection()
      {
        translate([-5, -20, 0]) cube([10, 7, WALL_THICKNESS]);
        cylinder(r=CASE_DIAMETER / 2 + WALL_THICKNESS, h=WALL_THICKNESS);
      }
    }
    // FFC
    translate([-5 - MECHANICAL_CLEARANCE, -19, 0]) rotate([10, 0, 0])  cube([10 + MECHANICAL_CLEARANCE * 2, 7, 2]);
  }
}

module case_top() {
  difference()
  {
    cylinder(r=CASE_DIAMETER / 2 + WALL_THICKNESS, h=CASE_HEIGHT);
    cylinder(r=CASE_DIAMETER / 2, h=CASE_HEIGHT + EPSILON);
    // FFC
    translate([-5 - MECHANICAL_CLEARANCE, -20, 0]) cube([10 + MECHANICAL_CLEARANCE * 2, 7, 1]);
  }
  translate([0, 0, CASE_HEIGHT]) dome(r=CASE_DIAMETER / 2 + WALL_THICKNESS, h=DOME_HEIGHT);
  // Insert pillars
  for (screw_location = SCREW_LOCATIONS)
    translate([screw_location[0], screw_location[1], 3]) cylinder(h=5, r=3);
  // stand-offs
  translate([9, -7.5, 3]) cylinder(h=5, r=1.5);
  translate([-9, -7.5, 3]) cylinder(h=5, r=1.5);

  translate([BUTTONS_LOCATIONS[0][0], -12, CASE_HEIGHT + DOME_HEIGHT - 1]) linear_extrude(1.2) import("lock.svg", center=true);
  translate([BUTTONS_LOCATIONS[1][0], -12, CASE_HEIGHT + DOME_HEIGHT - 1]) linear_extrude(1.2) import("unlock.svg", center=true);
}

module buttons() {
  for (button_location = BUTTONS_LOCATIONS)
  {
    translate([button_location[0], button_location[1], 5.6])
    difference()
    {
      union()
      {
        cylinder(h=4.9, r=2 - MECHANICAL_CLEARANCE);
        cylinder(h=1, r=3);
      }
      cylinder(h=4.2, r=1.5);
    }
  }
}

module cutouts() {
  color("pink", 0.5)
  {
    // USB-C
    translate([0.08, 8.35, WALL_THICKNESS]) round_cube([9, 3.5, 10], 1.2);
    // Buttons
    for (button_location = BUTTONS_LOCATIONS)
      translate([button_location[0], button_location[1], 7]) cylinder(h=3, r=2);
  }
}

module hardware()
{
  for (screw_location = SCREW_LOCATIONS)
  {
    translate([screw_location[0], screw_location[1], 0]) m2_countersunk_screw(5.5);
    translate([screw_location[0], screw_location[1], 3]) m2_insert();
  }
}

difference()
{
  union()
  {
    if (show_top) case_top();
    if (show_bottom) case_bottom();
  }
  pcb();
  cutouts();
  hardware();
}

difference()
{
  if (show_buttons) buttons();
  //pcb();
}

if ($preview)
{
  pcb();
  cutouts();
  hardware();
}

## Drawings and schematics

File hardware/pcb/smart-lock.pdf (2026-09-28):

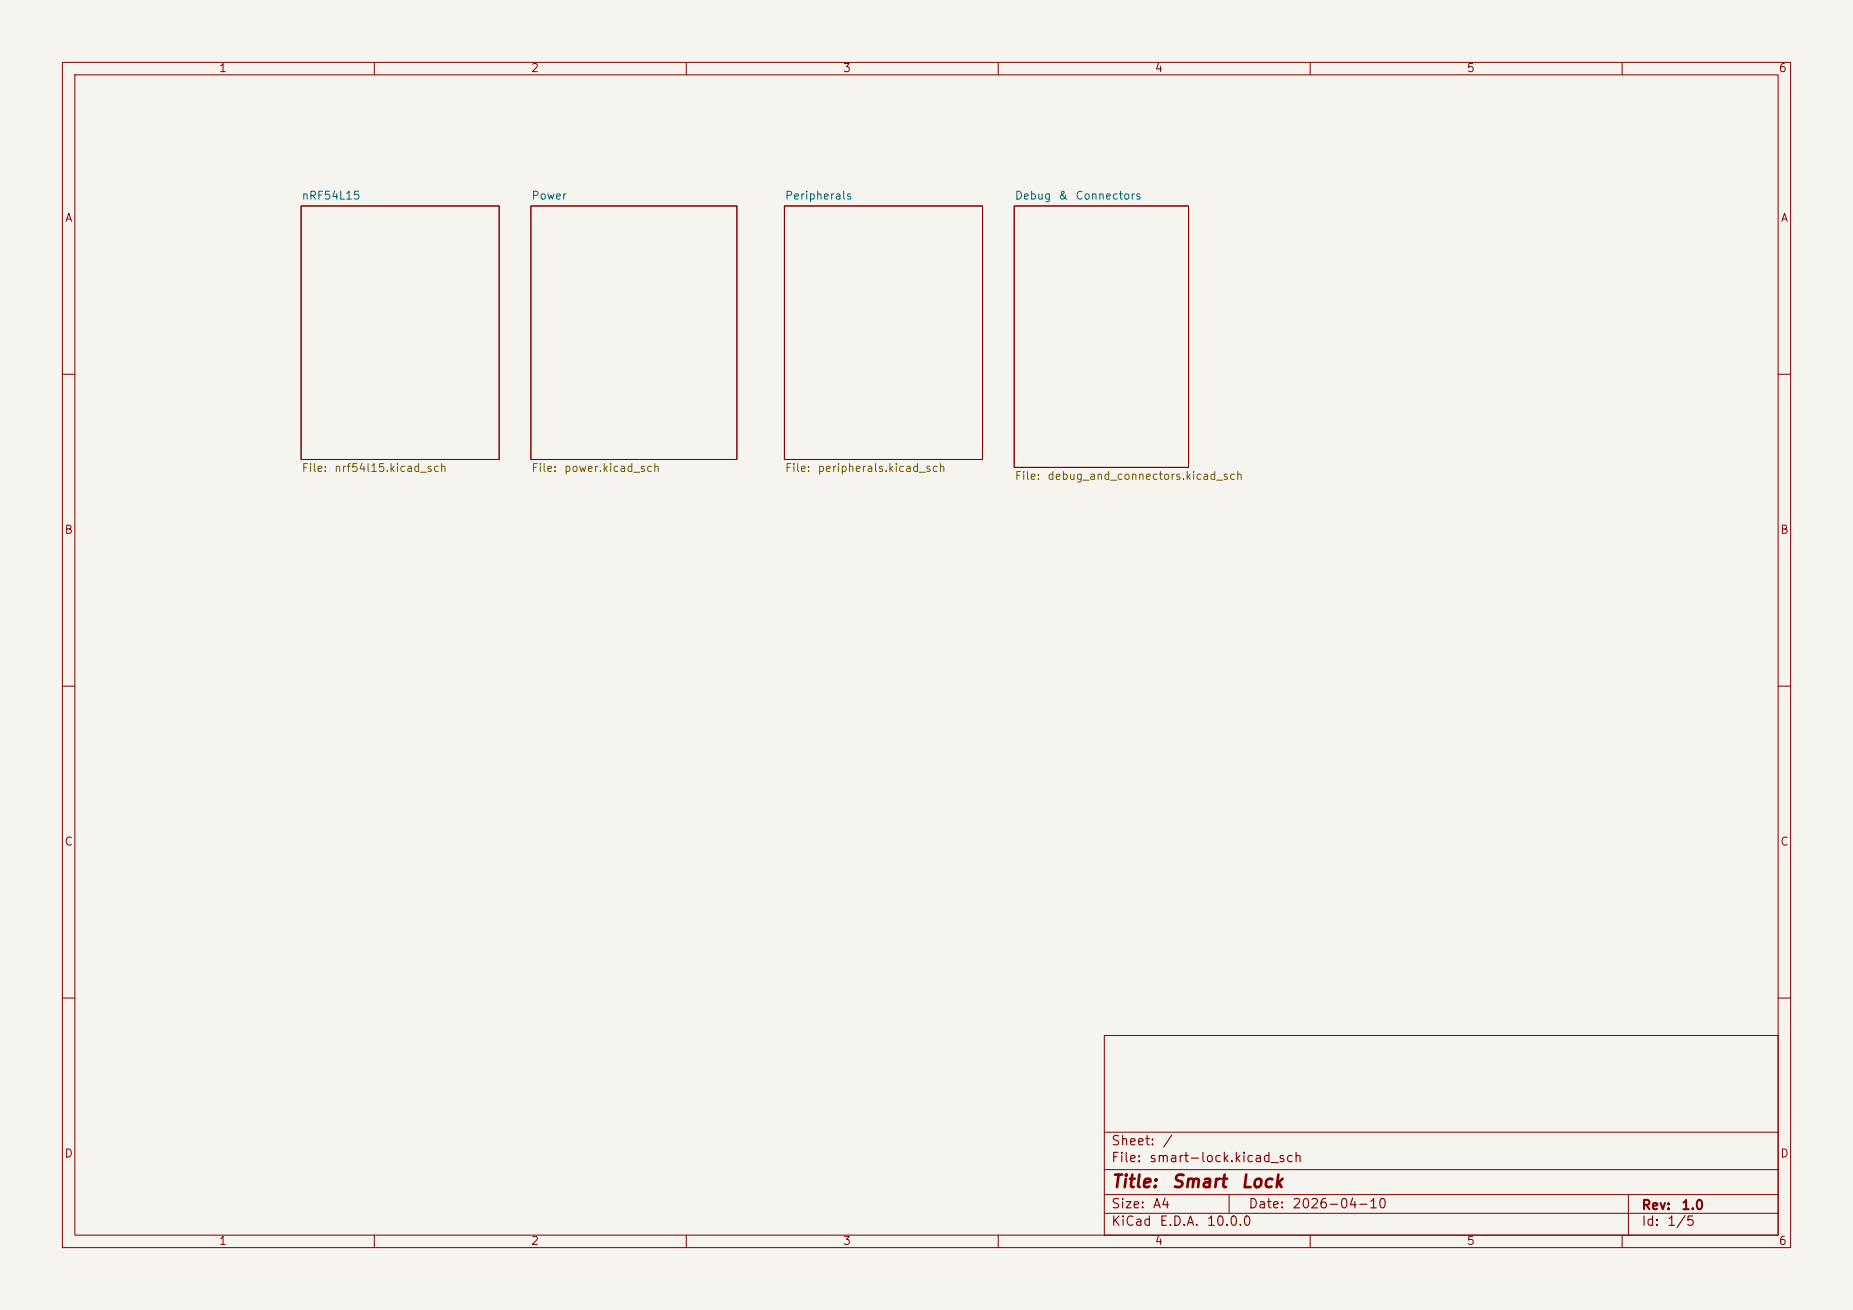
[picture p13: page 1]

Debug & Connectors File: debug_and_connectors.kicad_sch Power File: power.kicad_sch

Size: A4 | Rev: 1.0

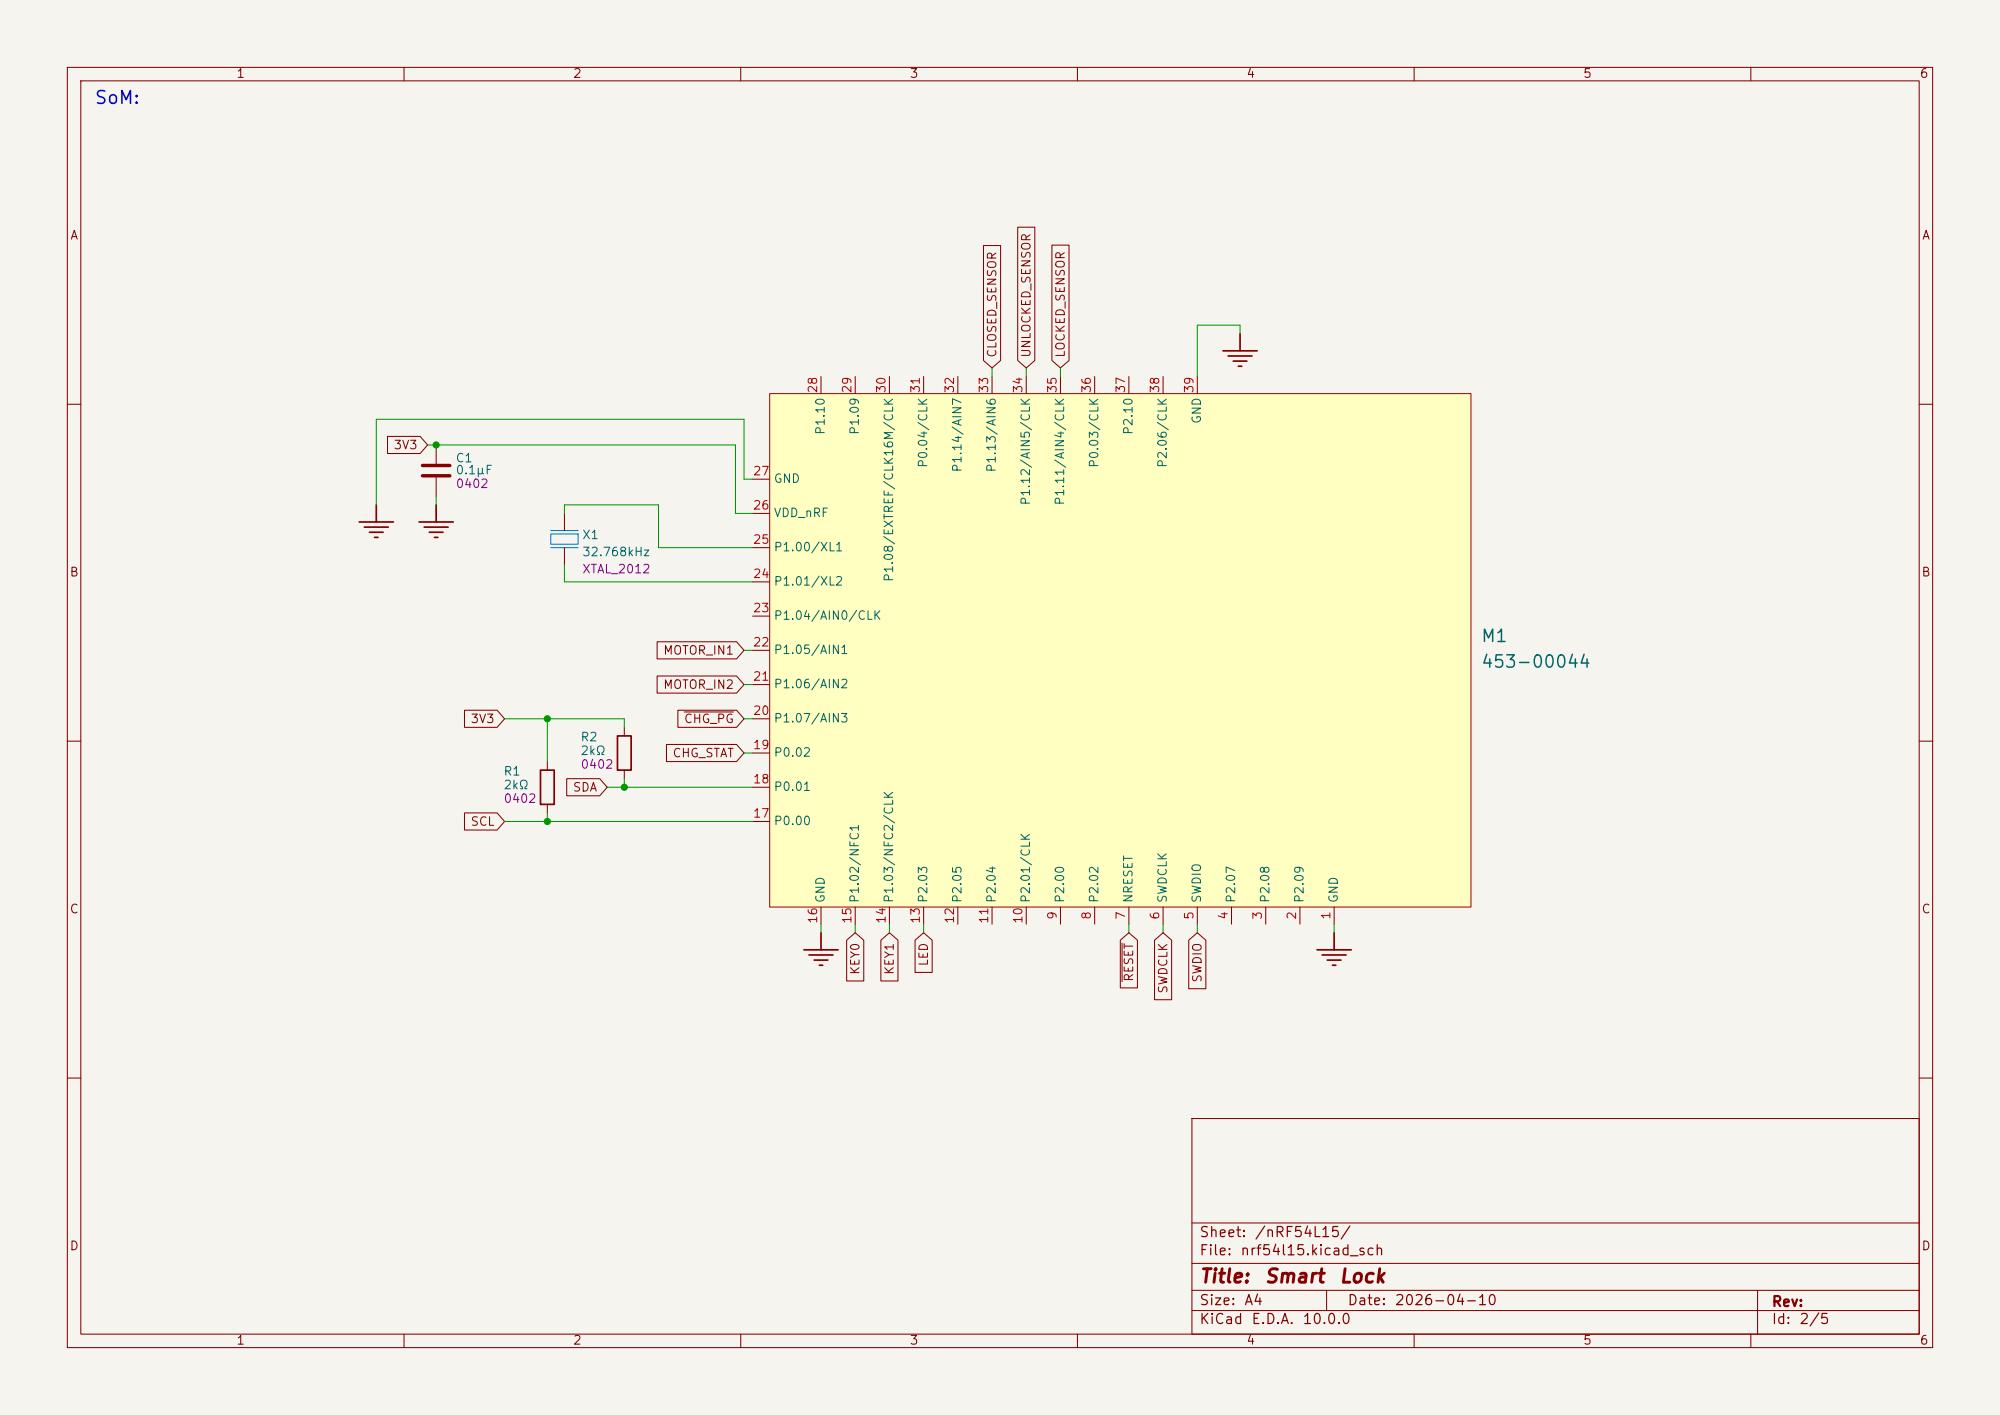
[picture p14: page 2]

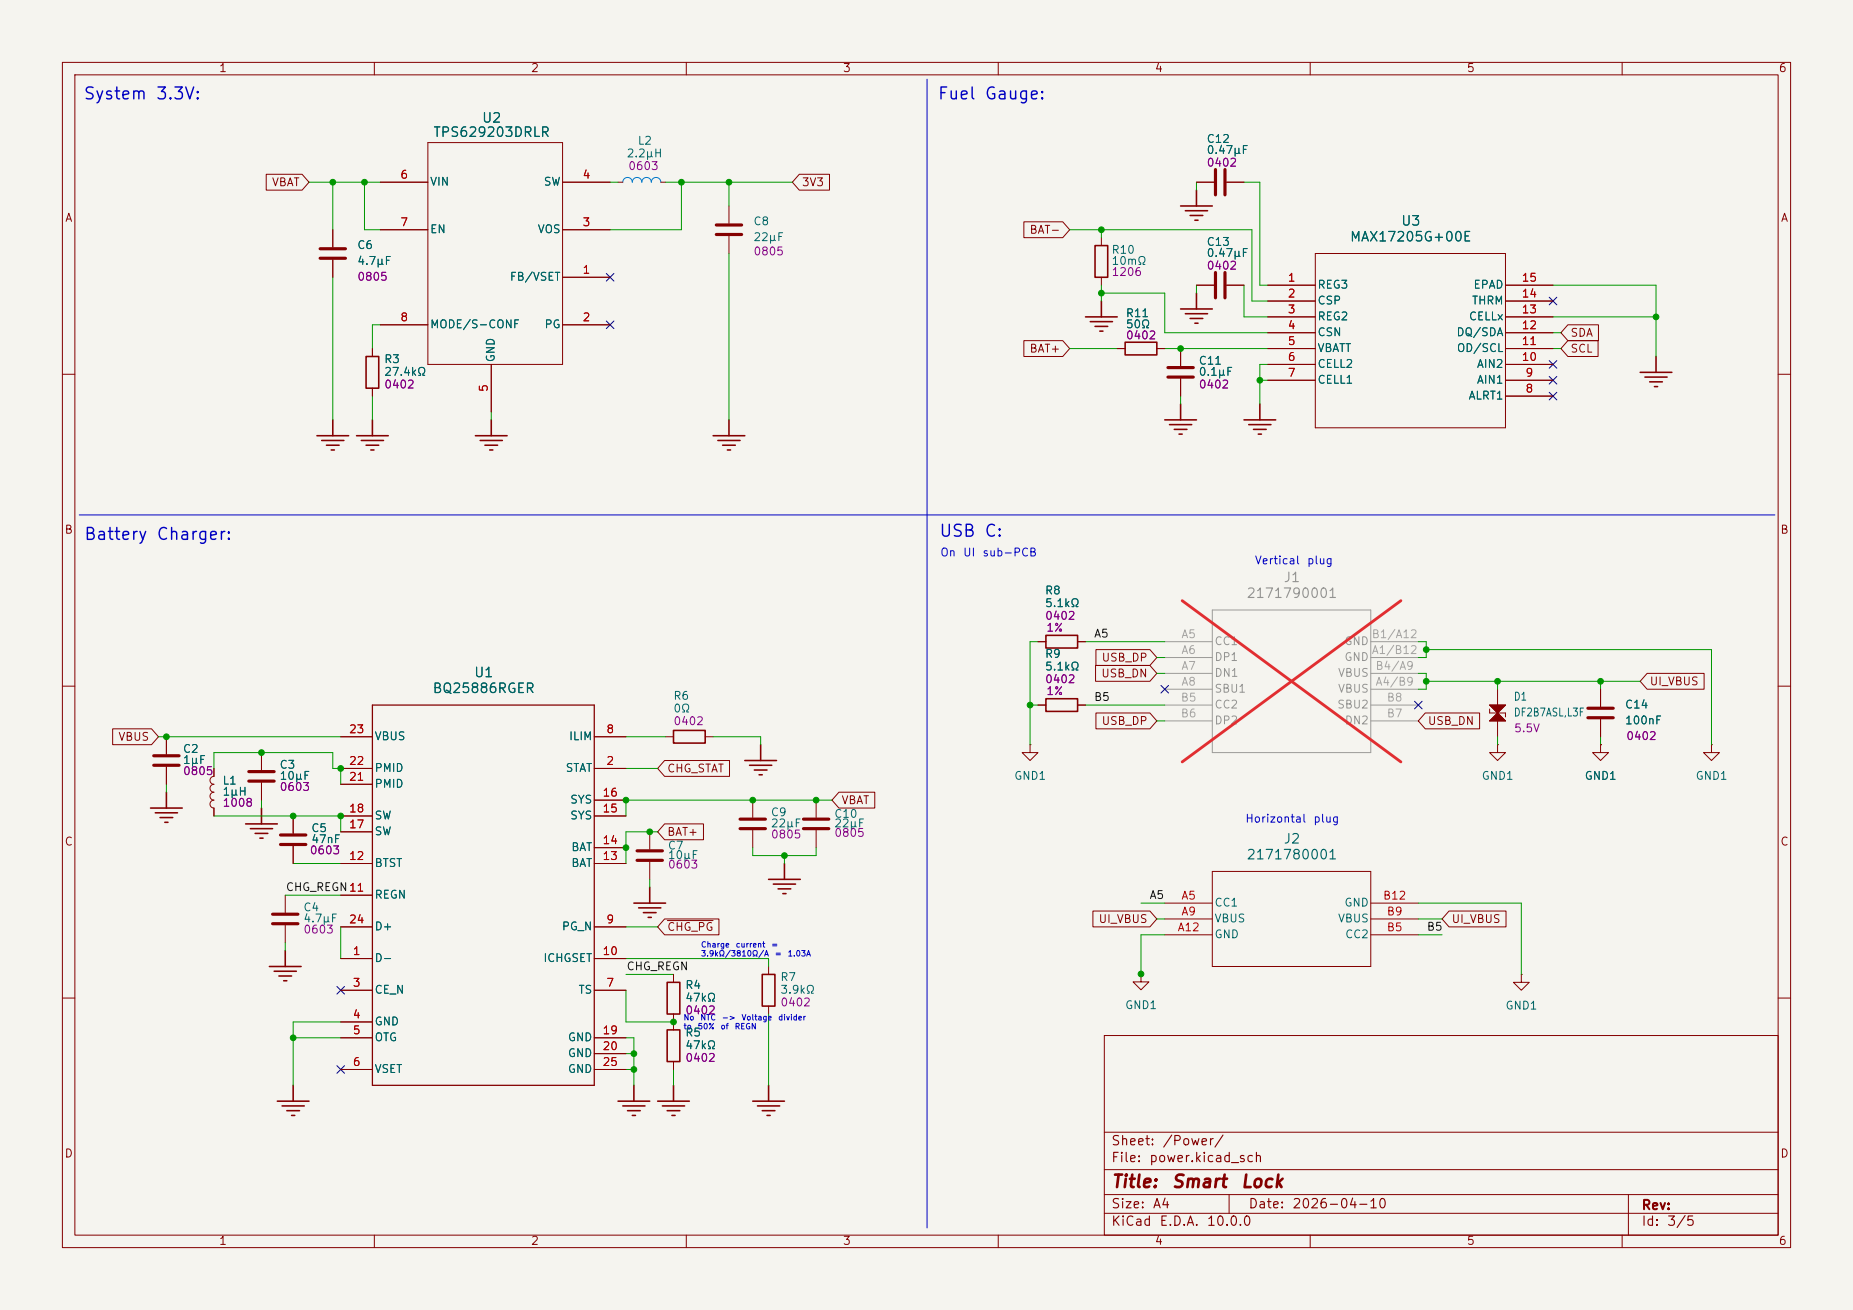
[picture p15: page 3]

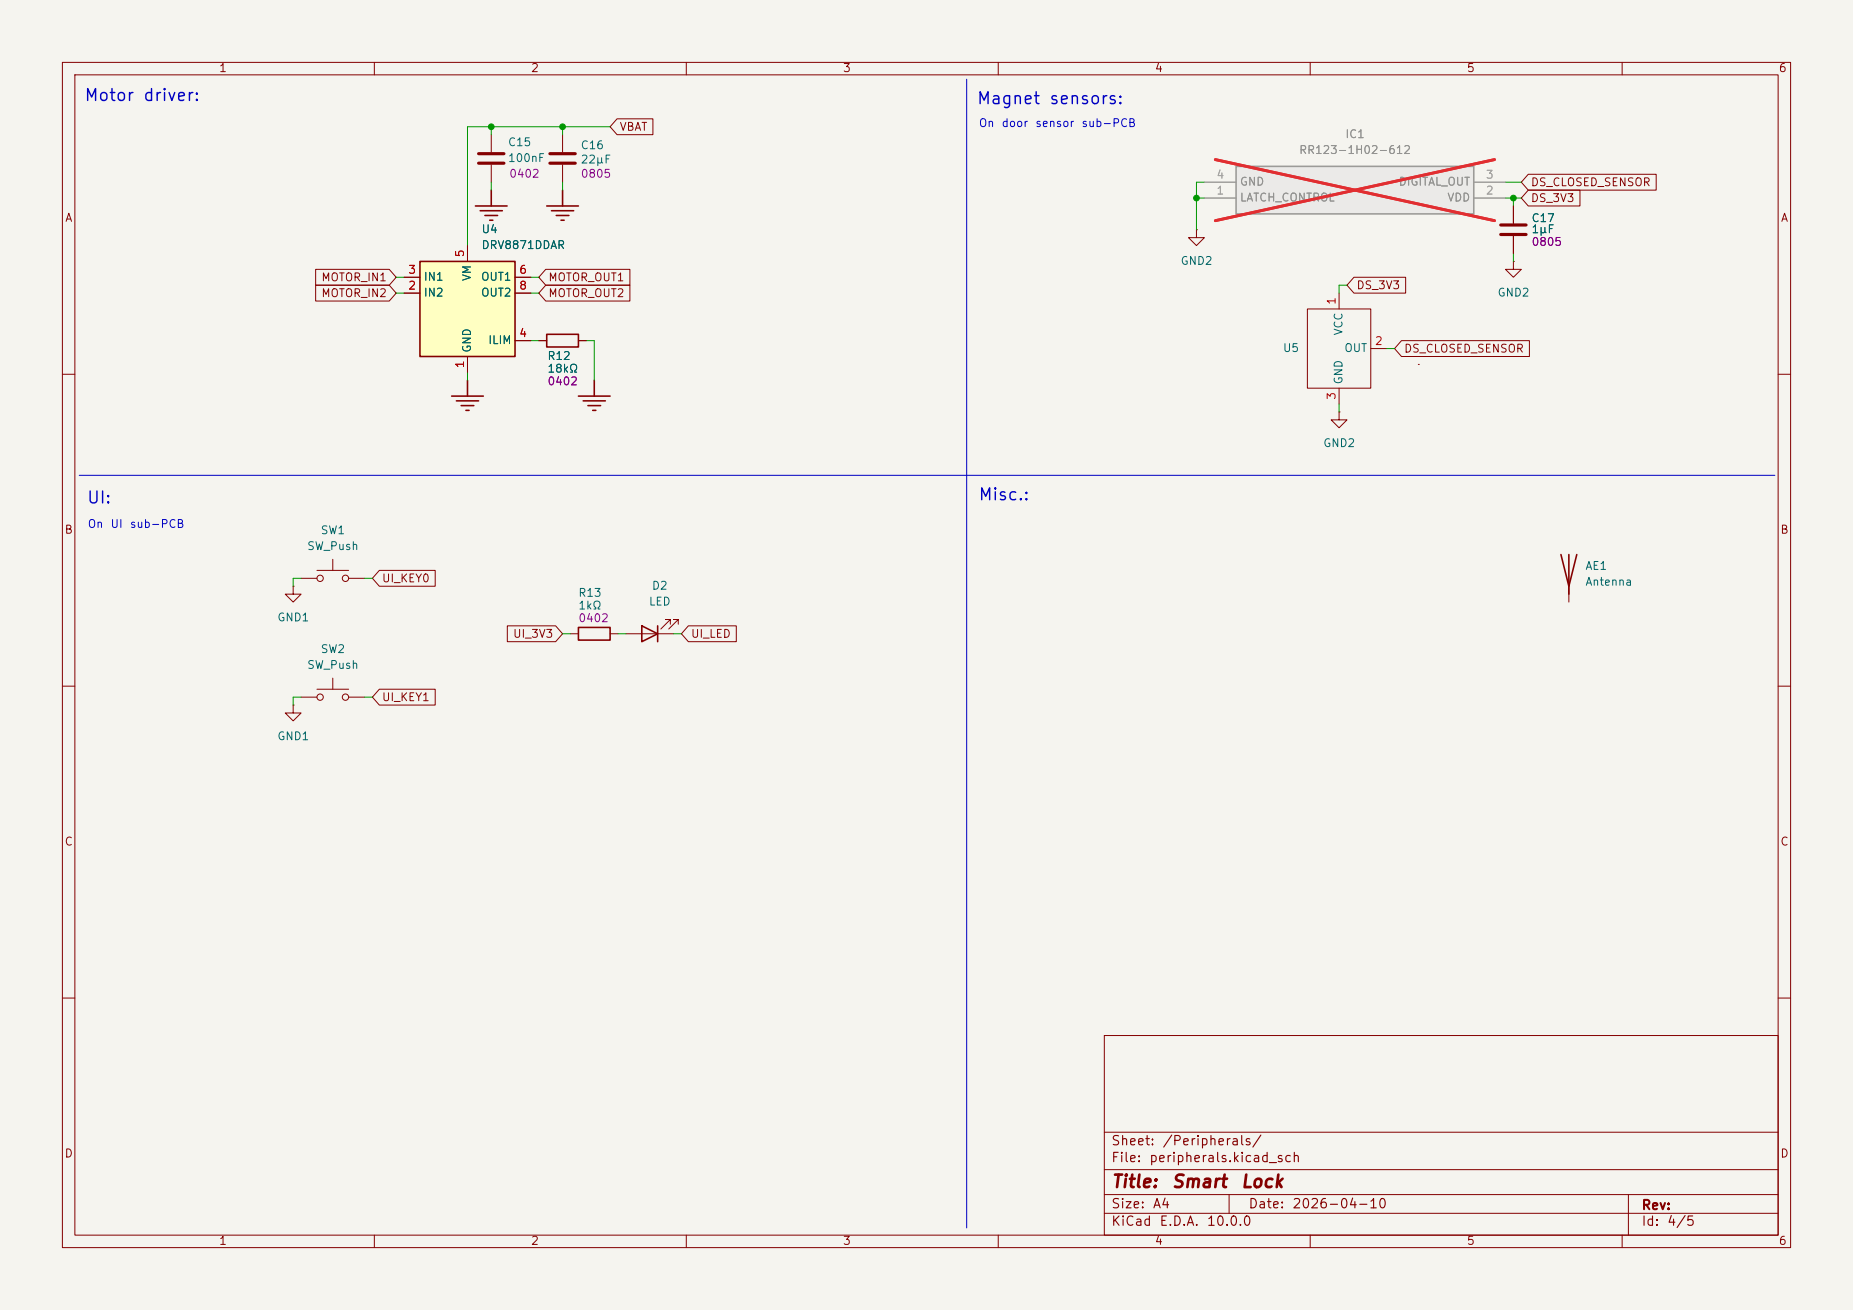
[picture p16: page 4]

DS_CLOSED_SENSOR Magnet sensors: On door sensor sub-PCB Misc.:

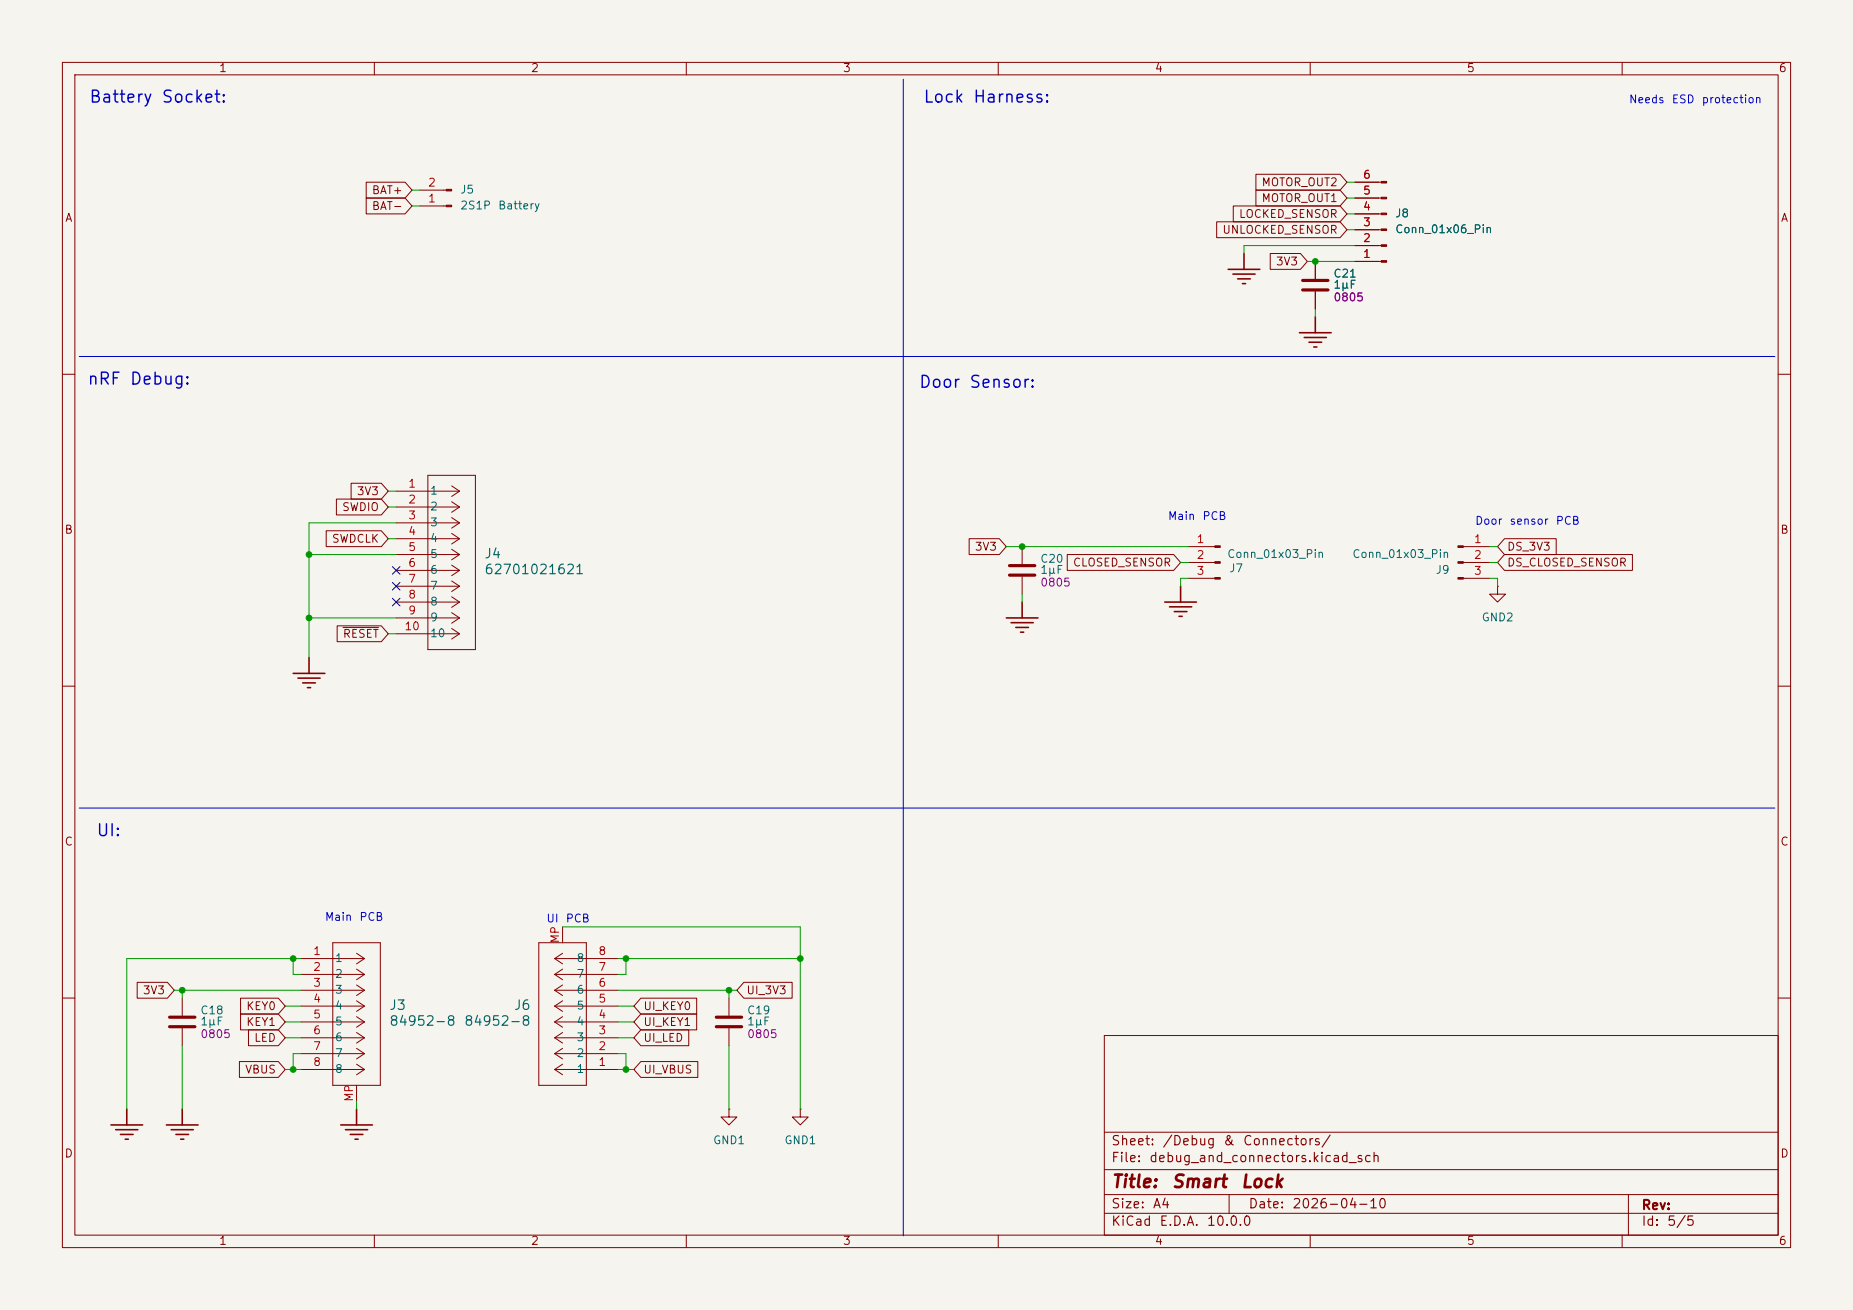
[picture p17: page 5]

Main PCB UI PCB UI:

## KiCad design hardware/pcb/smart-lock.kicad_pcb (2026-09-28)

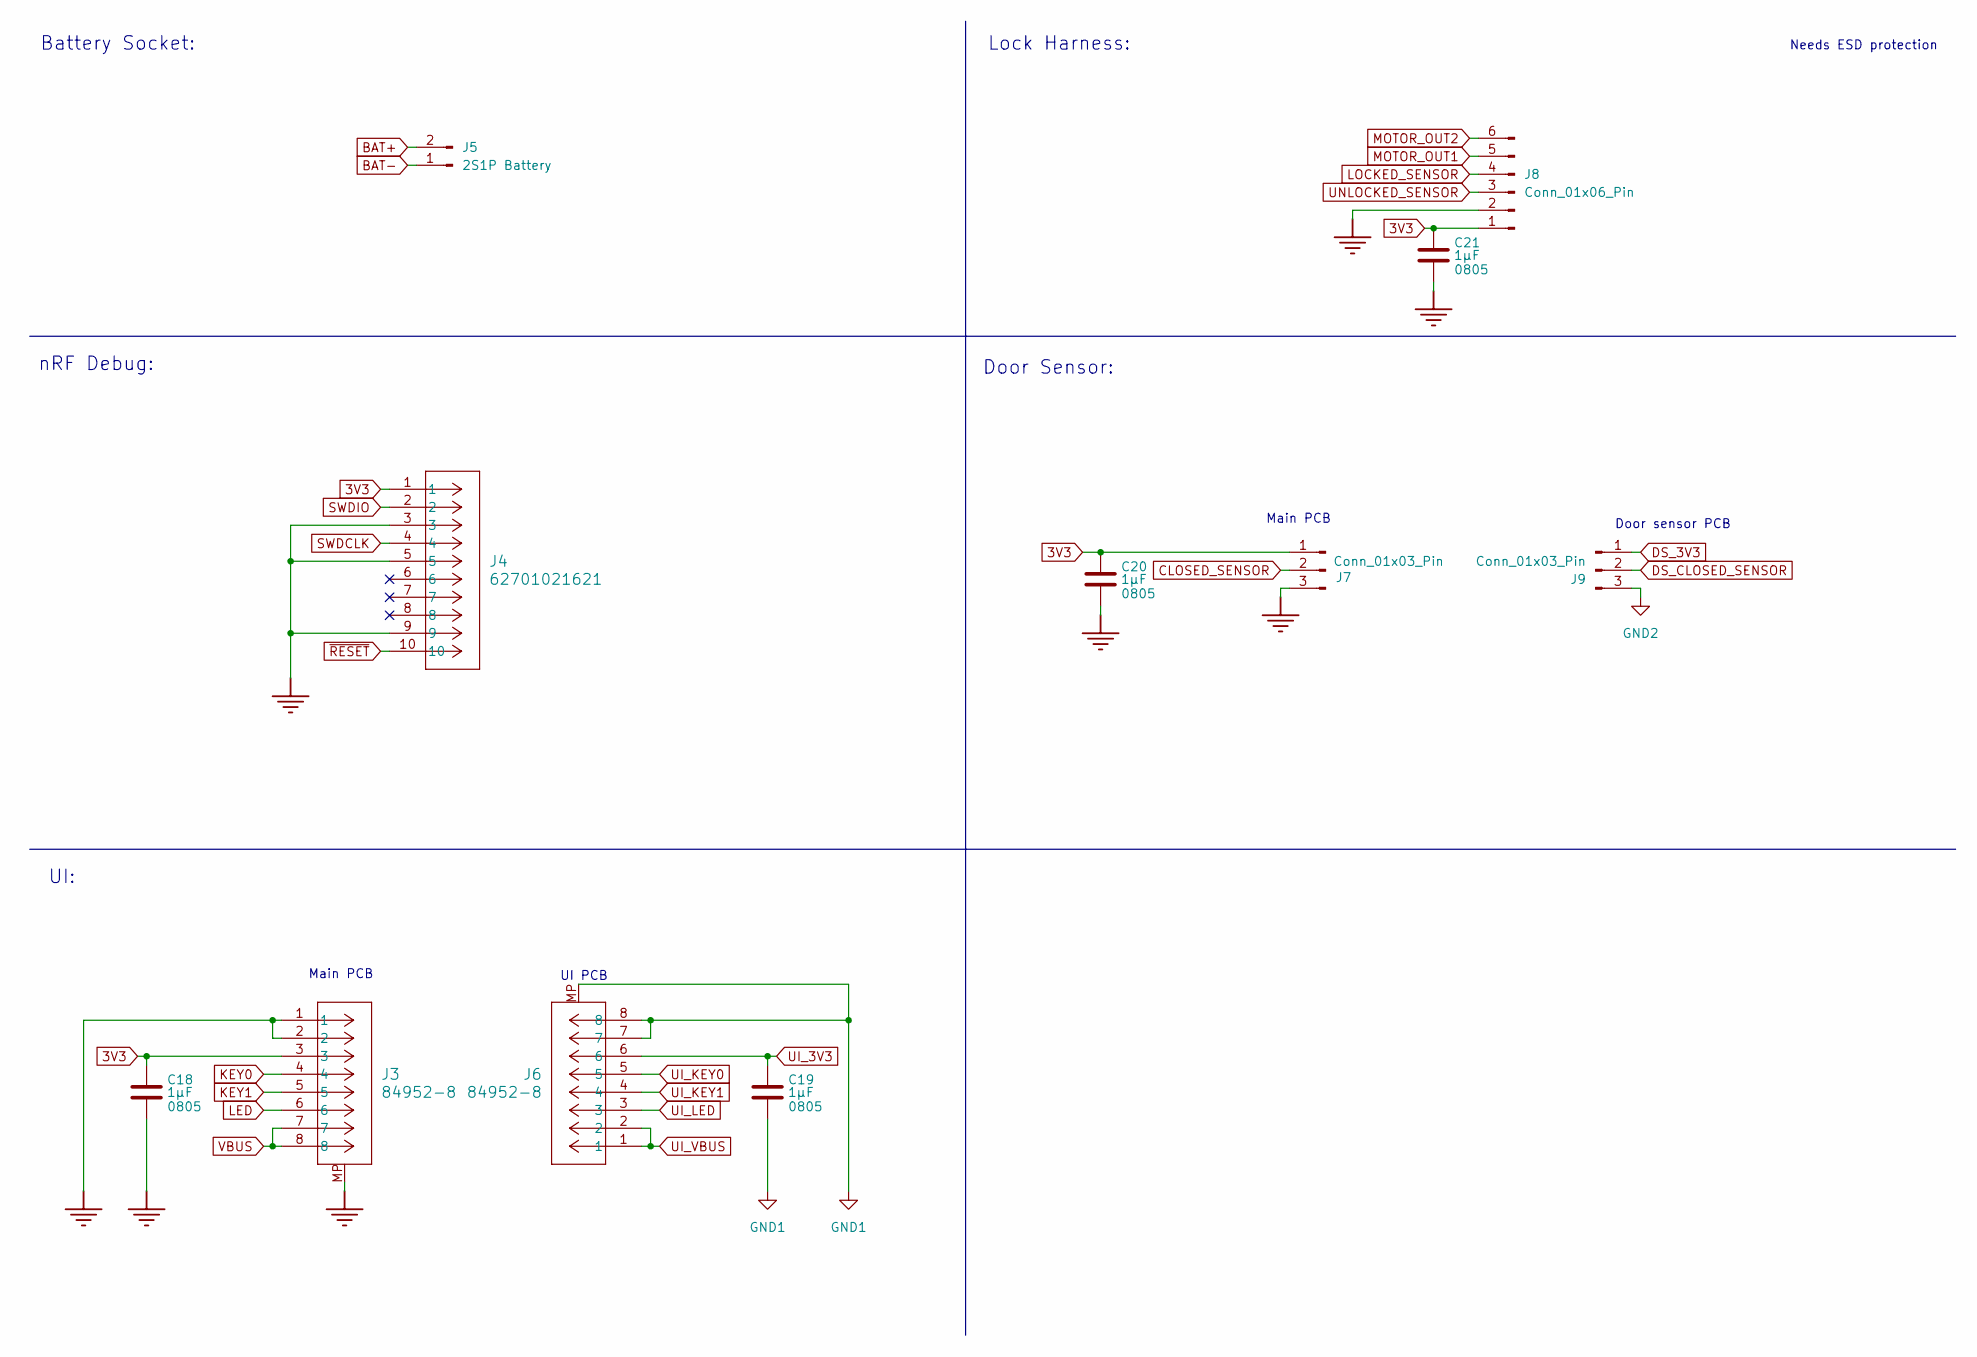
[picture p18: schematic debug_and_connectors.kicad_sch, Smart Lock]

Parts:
C18, C19, C20, C21: 1µF; C_0805_2012Metric; Voltage 10V; MANUFACTURER PART NUMBER GRM21BR71A105KA01K
J3, J6: 84952-8; CON8_SMT-RA_FCC-FPC2; MANUFACTURER PART NUMBER 84952-8
J4: 62701021621; CONN_62701021621_WRE; MANUFACTURER PART NUMBER 62701021621
J5: 2S1P Battery; JST_XH_S2B-XH-A_1x02_P2.50mm_Horizontal; MANUFACTURER PART NUMBER S2B-XH-A(LF)(SN)
J7: Conn_01x03_Pin; JST_XH_S3B-XH-A_1x03_P2.50mm_Horizontal; MANUFACTURER PART NUMBER S3B-XH-A(LF)(SN)
J8: Conn_01x06_Pin; JST_XH_S6B-XH-A_1x06_P2.50mm_Horizontal; MANUFACTURER PART NUMBER S6B-XH-A(LF)(SN)
J9: Conn_01x03_Pin; JST_XH_B3B-XH-A_1x03_P2.50mm_Vertical; MANUFACTURER PART NUMBER B3B-XH-A(LF)(SN)

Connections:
3V3: C18.1, C20.1, C21.1, J3.3, J4.1, J7.1, J8.1; also elsewhere on the board
BAT+: J5.2; also elsewhere on the board
BAT-: J5.1; also elsewhere on the board
CLOSED_SENSOR: J7.2; also elsewhere on the board
DS_3V3: J9.1; also elsewhere on the board
DS_CLOSED_SENSOR: J9.2; also elsewhere on the board
GND: C18.2, C20.2, C21.2, J3.1, J3.2, J3.MP, J4.3, J4.5, J4.9, J7.3, J8.2; also elsewhere on the board
GND1: C19.2, J6.7, J6.8, J6.MP; also elsewhere on the board
GND2: J9.3; also elsewhere on the board
KEY0: J3.4; also elsewhere on the board
KEY1: J3.5; also elsewhere on the board
LED: J3.6; also elsewhere on the board
LOCKED_SENSOR: J8.4; also elsewhere on the board
MOTOR_OUT1: J8.5; also elsewhere on the board
MOTOR_OUT2: J8.6; also elsewhere on the board
SWDCLK: J4.4; also elsewhere on the board
SWDIO: J4.2; also elsewhere on the board
UI_3V3: C19.1, J6.6; also elsewhere on the board
UI_KEY0: J6.5; also elsewhere on the board
UI_KEY1: J6.4; also elsewhere on the board
UI_LED: J6.3; also elsewhere on the board
UI_VBUS: J6.1, J6.2; also elsewhere on the board
UNLOCKED_SENSOR: J8.3; also elsewhere on the board
VBUS: J3.7, J3.8; also elsewhere on the board
~RESET: J4.10; also elsewhere on the board

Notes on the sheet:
Needs ESD protection
UI:
Main PCB
nRF Debug:
UI PCB
Battery Socket:
Door sensor PCB
Door Sensor:
Lock Harness:

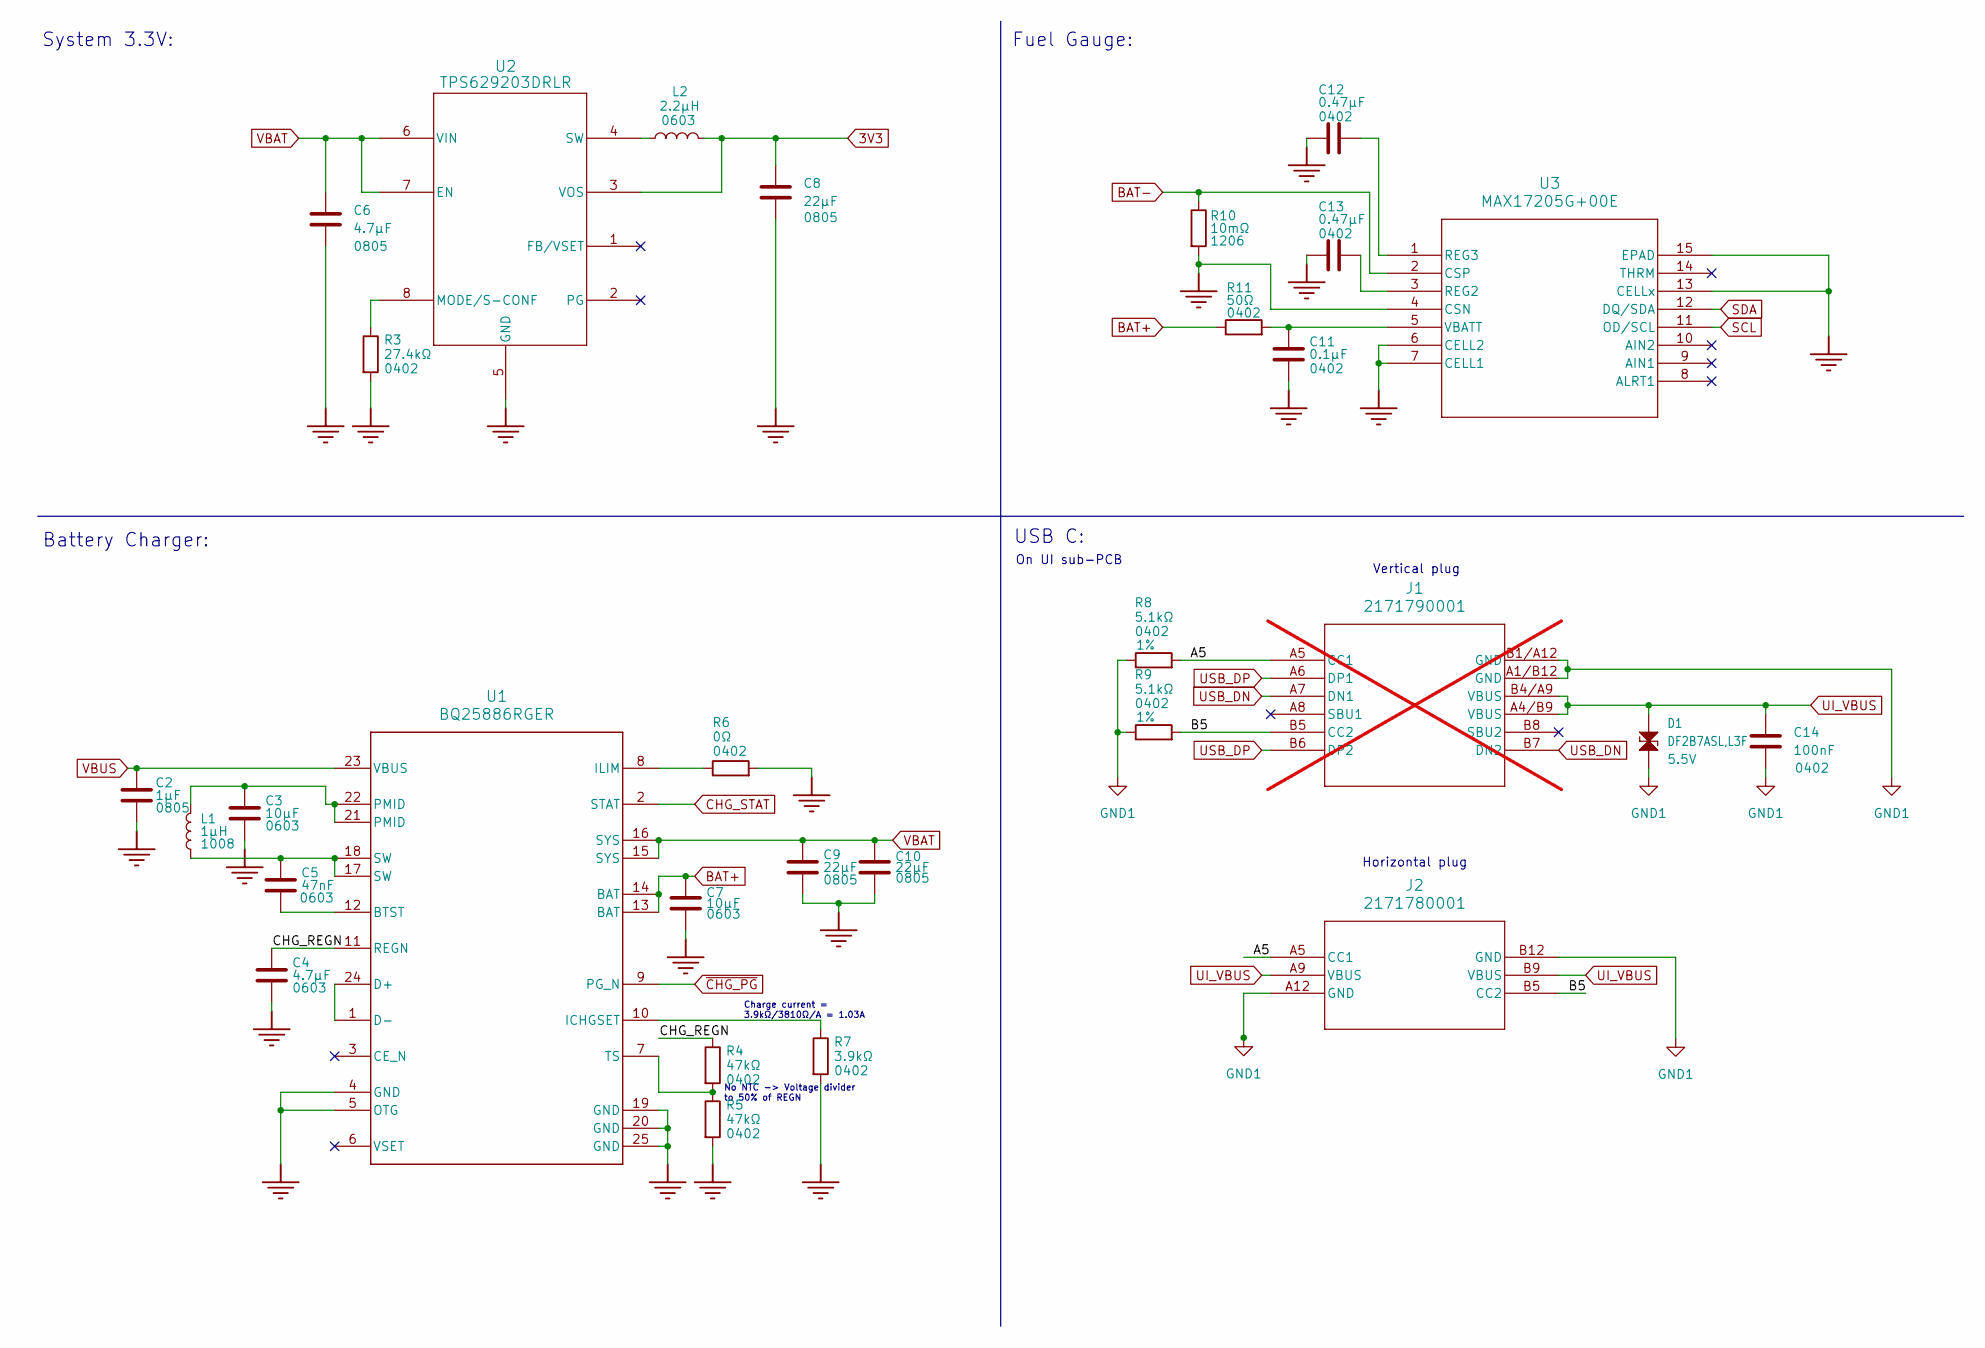
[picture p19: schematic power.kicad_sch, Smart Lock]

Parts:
C2: 1µF; C_0805_2012Metric; Voltage 10V; MANUFACTURER PART NUMBER GRM21BR71A105KA01K
C3, C7: 10µF; C_0603_1608Metric; Voltage 16V; MANUFACTURER PART NUMBER GRM188R61C106MA73D
C4: 4.7µF; C_0603_1608Metric; Voltage 16V; MANUFACTURER PART NUMBER GRT188C71C475KE13D
C5: 47nF; C_0603_1608Metric; Voltage 25V; MANUFACTURER PART NUMBER GCM188R71E473KA37D
C6: 4.7µF; C_0805_2012Metric; Voltage 16V; MANUFACTURER PART NUMBER GRM21BR71C475KE51L
C8, C9, C10: 22µF; C_0805_2012Metric; Voltage 25V; MANUFACTURER PART NUMBER GRM21BR61E226ME44L
C11: 0.1µF; C_0402_1005Metric; Voltage 25V; MANUFACTURER PART NUMBER GRM155R71E104KE14J
C12, C13: 0.47µF; C_0402_1005Metric; Voltage 6.3V; MANUFACTURER PART NUMBER GRM155R60J474KE19D
C14: 100nF; C_0402_1005Metric; Voltage 16V; MANUFACTURER PART NUMBER GRM155R71C104KA88D
D1: DF2B7ASL,L3F; D_0201_0603Metric; Voltage 5.5V; MANUFACTURER PART NUMBER DF2B7ASL,L3F
J1: 2171790001; 2171790001_MOL; MANUFACTURER PART NUMBER 2171790001; not fitted
J2: 2171780001; CONN_2171780001_MOL; MANUFACTURER PART NUMBER 2171780001
L1: 1µH; L_1008_2520Metric; MANUFACTURER PART NUMBER DFE252012F-1R0M=P2
L2: 2.2µH; INDC1608X06L; MANUFACTURER PART NUMBER MLZ1608A2R2WT000
R3: 27.4kΩ; R_0402_1005Metric; MANUFACTURER PART NUMBER RC0402FR-1327K4L
R4, R5: 47kΩ; R_0402_1005Metric; MANUFACTURER PART NUMBER RC0402FR-0747KL
R6: 0Ω; R_0402_1005Metric; MANUFACTURER PART NUMBER RC0402JR-070RL
R7: 3.9kΩ; R_0402_1005Metric; MANUFACTURER PART NUMBER RC0402FR-073K9L
R8, R9: 5.1kΩ; R_0402_1005Metric; Tolerance 1%; MANUFACTURER PART NUMBER RC0402FR-075K1L
R10: 10mΩ; R_1206_3216Metric; MANUFACTURER PART NUMBER PE1206DRM7W0R01L
R11: 50Ω; R_0402_1005Metric; MANUFACTURER PART NUMBER RC0402JR-0750RL
U1: BQ25886RGER; RGE0024H_NV; MANUFACTURER PART NUMBER BQ25886RGER
U2: TPS629203DRLR; SOT-5x3_DRL0008A_TEX-L; MANUFACTURER PART NUMBER TPS629203DRLR
U3: MAX17205G+00E; MAX17205G; MANUFACTURER PART NUMBER MAX17205G+00E

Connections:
3V3: C8.1, L2.2, U2.3 (VOS); also elsewhere on the board
/Power/A5: J1.A5 (CC1), J2.A5 (CC1), R8.2
/Power/B5: J1.B5 (CC2), J2.B5 (CC2), R9.2
/Power/CHG_REGN: C4.1, R4.1, U1.11 (REGN)
BAT+: C7.1, R11.1, U1.13 (BAT), U1.14 (BAT); also elsewhere on the board
BAT-: R10.1, U3.2 (CSP); also elsewhere on the board
CHG_STAT: U1.2 (STAT); also elsewhere on the board
GND: C2.2, C3.2, C4.2, C6.2, C7.2, C8.2, C9.2, C10.2, C11.2, C12.1, C13.1, R3.2, R5.2, R6.2, R7.2, R10.2, U1.4 (GND), U1.5 (OTG), U1.19 (GND), U1.20 (GND), U1.25 (GND), U2.5 (GND), U3.4 (CSN), U3.6 (CELL2), U3.7 (CELL1), U3.13 (CELLx), U3.15 (EPAD); also elsewhere on the board
GND1: C14.2, D1.1, J1.A1/B12 (GND), J1.B1/A12 (GND), J2.A12 (GND), J2.B12 (GND), R8.1, R9.1; also elsewhere on the board
unnamed: C3.1, L1.2, U1.21 (PMID), U1.22 (PMID)
unnamed: C5.1, L1.1, U1.17 (SW), U1.18 (SW)
unnamed: C5.2, U1.12 (BTST)
unnamed: U1.1 (D-), U1.24 (D+)
unnamed: R7.1, U1.10 (ICHGSET)
unnamed: R6.1, U1.8 (ILIM)
unnamed: R4.2, R5.1, U1.7 (TS)
unnamed: R3.1, U2.8 (MODE/S-CONF)
unnamed: L2.1, U2.4 (SW)
unnamed: C13.2, U3.3 (REG2)
unnamed: C12.2, U3.1 (REG3)
unnamed: C11.1, R11.2, U3.5 (VBATT)
SCL: U3.11 (OD/SCL); also elsewhere on the board
SDA: U3.12 (DQ/SDA); also elsewhere on the board
UI_VBUS: C14.1, D1.2, J1.A4/B9 (VBUS), J1.B4/A9 (VBUS), J2.A9 (VBUS), J2.B9 (VBUS); also elsewhere on the board
USB_DN: J1.A7 (DN1), J1.B7 (DN2)
USB_DP: J1.A6 (DP1), J1.B6 (DP2)
VBAT: C6.1, C9.1, C10.1, U1.15 (SYS), U1.16 (SYS), U2.6 (VIN), U2.7 (EN); also elsewhere on the board
VBUS: C2.1, U1.23 (VBUS); also elsewhere on the board
~CHG_PG: U1.9 (PG_N); also elsewhere on the board

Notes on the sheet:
Battery Charger:
Vertical plug
No NTC -> Voltage divider to 50% of REGN
On UI sub-PCB
USB C:
Horizontal plug
System 3.3V:
Fuel Gauge:
Charge current = 3.9kΩ/3810Ω/A = 1.03A

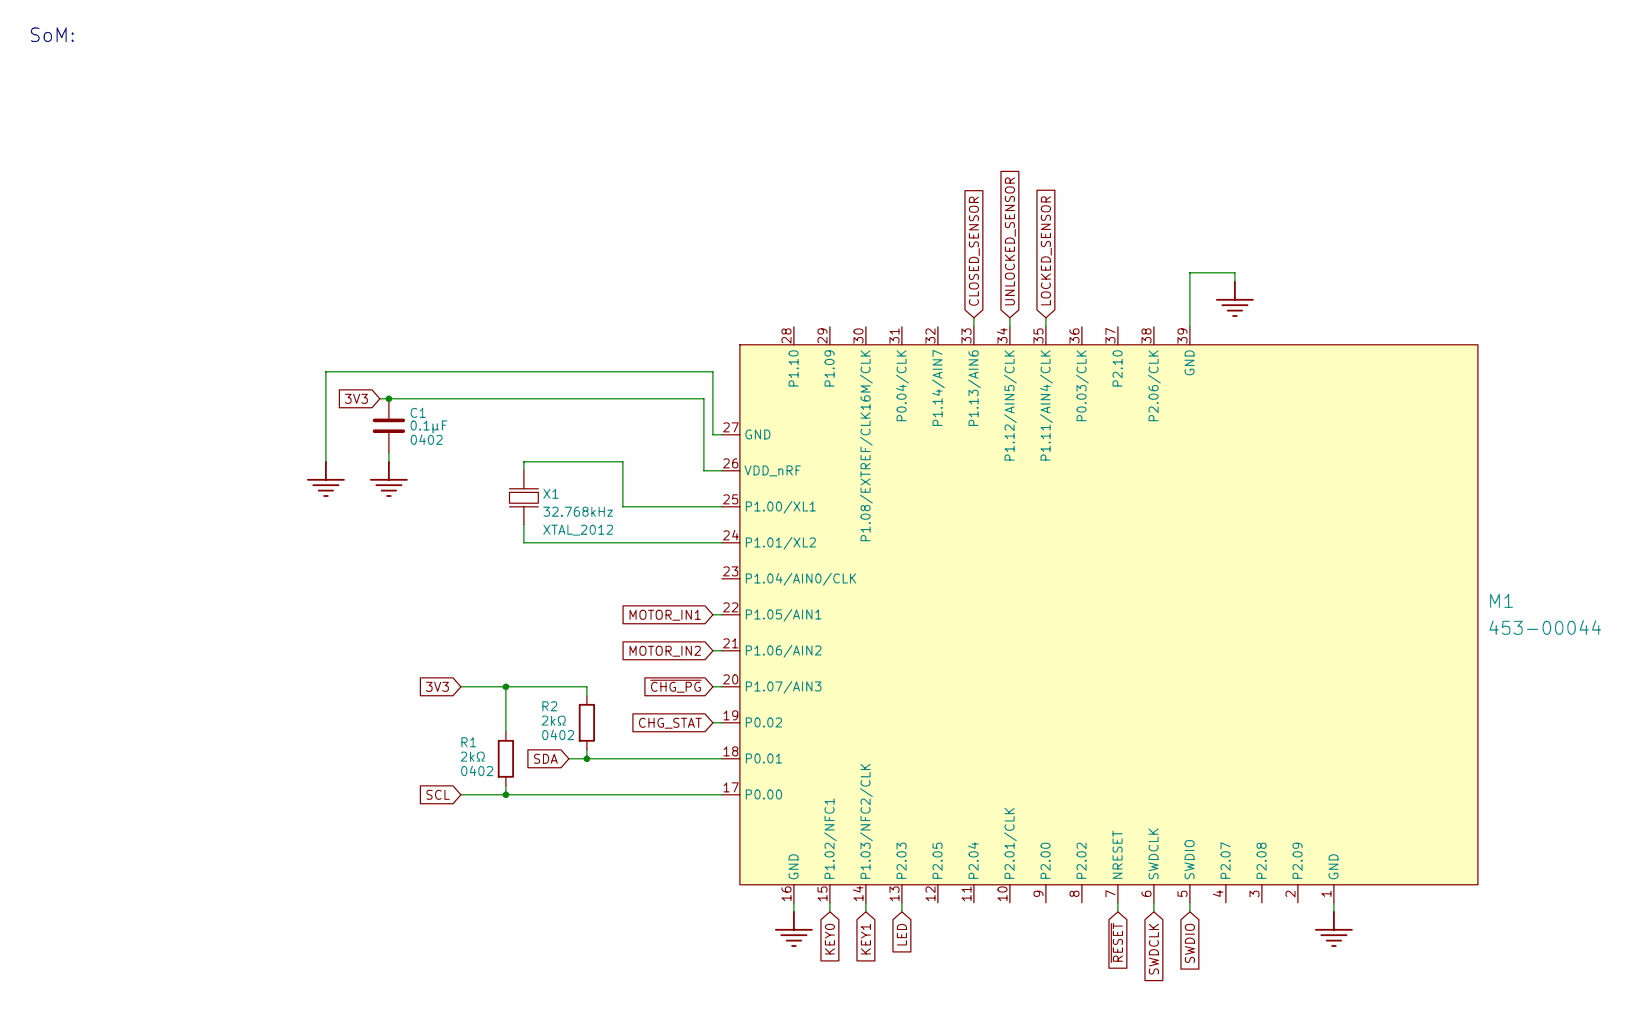
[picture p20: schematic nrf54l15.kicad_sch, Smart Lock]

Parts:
C1: 0.1µF; C_0402_1005Metric; Voltage 25V; MANUFACTURER PART NUMBER GRM155R71E104KE14J
M1: 453-00044; MANUFACTURER PART NUMBER 453-00044R
R1, R2: 2kΩ; R_0402_1005Metric; MANUFACTURER PART NUMBER RC0402FR-072KL
X1: 32.768kHz; XTAL_2012; MANUFACTURER PART NUMBER 9HT11-32.768KDZC-T

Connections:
3V3: C1.1, M1.26 (VDD_nRF), R1.1, R2.1; also elsewhere on the board
CHG_STAT: M1.19 (P0.02); also elsewhere on the board
CLOSED_SENSOR: M1.33 (P1.13/AIN6); also elsewhere on the board
GND: C1.2, M1.1 (GND), M1.16 (GND), M1.27 (GND), M1.39 (GND); also elsewhere on the board
KEY0: M1.15 (P1.02/NFC1); also elsewhere on the board
KEY1: M1.14 (P1.03/NFC2/CLK); also elsewhere on the board
LED: M1.13 (P2.03); also elsewhere on the board
LOCKED_SENSOR: M1.35 (P1.11/AIN4/CLK); also elsewhere on the board
MOTOR_IN1: M1.22 (P1.05/AIN1); also elsewhere on the board
MOTOR_IN2: M1.21 (P1.06/AIN2); also elsewhere on the board
unnamed: M1.25 (P1.00/XL1), X1.2 (out)
unnamed: M1.24 (P1.01/XL2), X1.1 (inp)
SCL: M1.17 (P0.00), R1.2; also elsewhere on the board
SDA: M1.18 (P0.01), R2.2; also elsewhere on the board
SWDCLK: M1.6 (SWDCLK); also elsewhere on the board
SWDIO: M1.5 (SWDIO); also elsewhere on the board
UNLOCKED_SENSOR: M1.34 (P1.12/AIN5/CLK); also elsewhere on the board
~CHG_PG: M1.20 (P1.07/AIN3); also elsewhere on the board
~RESET: M1.7 (NRESET); also elsewhere on the board

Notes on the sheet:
SoM:

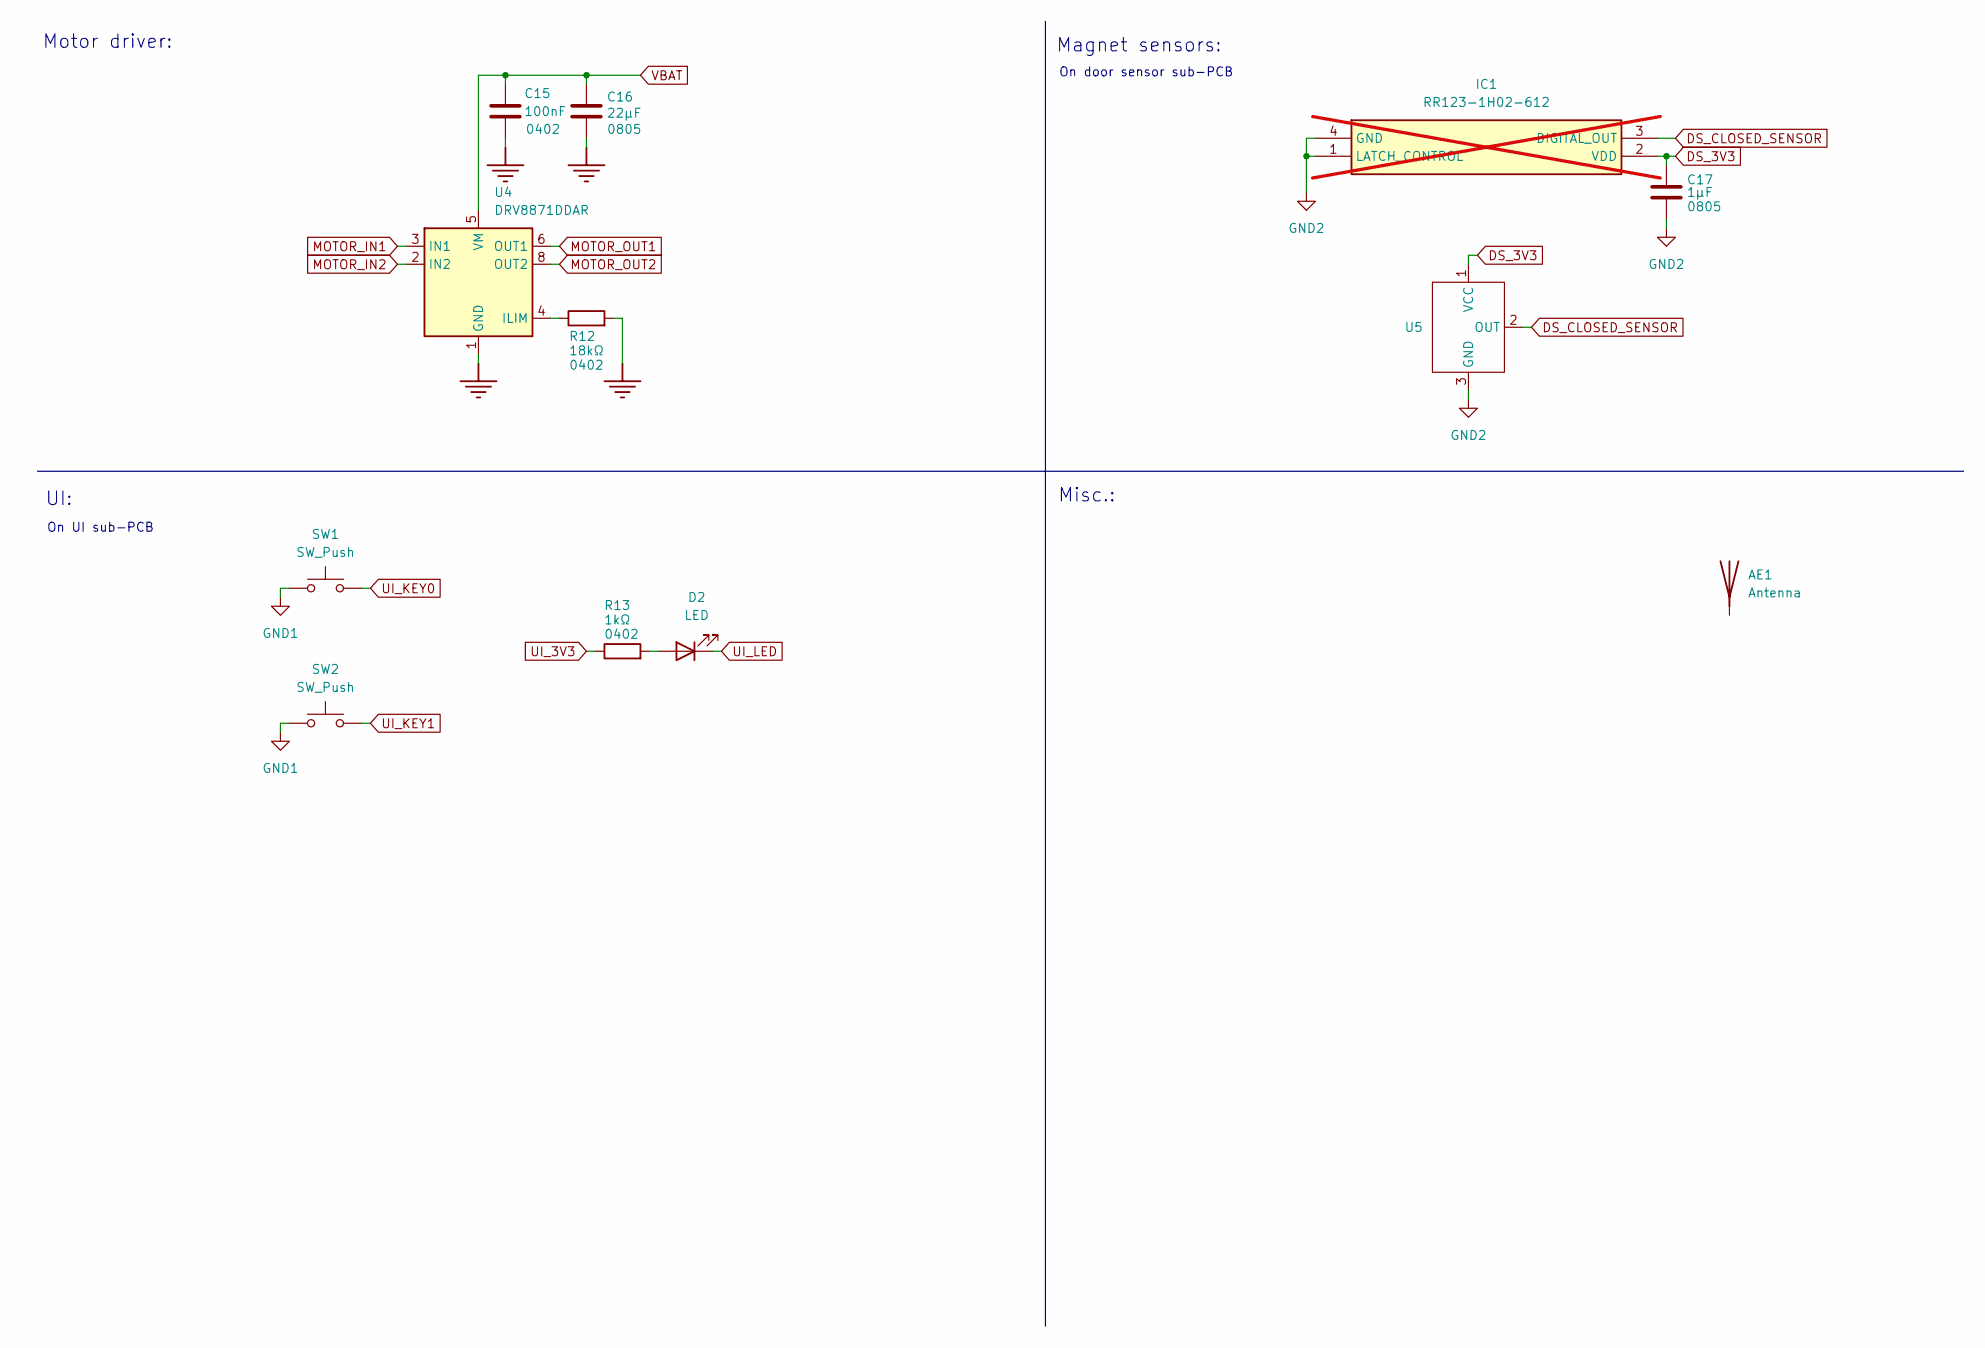
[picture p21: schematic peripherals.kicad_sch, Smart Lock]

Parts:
AE1: Antenna; MANUFACTURER PART NUMBER 2344656-6
C15: 100nF; C_0402_1005Metric; Voltage 16V; MANUFACTURER PART NUMBER GRM155R71C104KA88D
C16: 22µF; C_0805_2012Metric; Voltage 25V; MANUFACTURER PART NUMBER GRM21BR61E226ME44L
C17: 1µF; C_0805_2012Metric; Voltage 10V; MANUFACTURER PART NUMBER GRM21BR71A105KA01K
D2: LED; LED_0603_1608Metric; MANUFACTURER PART NUMBER TLMS1000-GS15
IC1: RR123-1H02-612; MANUFACTURER PART NUMBER RR123-1H02-612; not fitted
R12: 18kΩ; R_0402_1005Metric; MANUFACTURER PART NUMBER RC0402FR-0718KL
R13: 1kΩ; R_0402_1005Metric; MANUFACTURER PART NUMBER RC0402FR-071KL
SW1, SW2: SW_Push; SW_SPST_PTS647_Sx70; MANUFACTURER PART NUMBER PTS647SK70SMTR2 LFS
U4: DRV8871DDAR; HSOP-8-1EP_3.9x4.9mm_P1.27mm_EP2.41x3.1mm; MANUFACTURER PART NUMBER DRV8871DDAR
U5: SOT-23; MANUFACTURER PART NUMBER SL353LT

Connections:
DS_3V3: C17.1, IC1.2 (VDD), U5.1 (VCC); also elsewhere on the board
DS_CLOSED_SENSOR: IC1.3 (DIGITAL_OUT), U5.2 (OUT); also elsewhere on the board
GND: C15.2, C16.2, R12.2, U4.1 (GND), U4.7 (GND), U4.9 (GND); also elsewhere on the board
GND1: SW1.1, SW2.1; also elsewhere on the board
GND2: C17.2, IC1.1 (LATCH_CONTROL), IC1.4 (GND), U5.3 (GND); also elsewhere on the board
MOTOR_IN1: U4.3 (IN1); also elsewhere on the board
MOTOR_IN2: U4.2 (IN2); also elsewhere on the board
MOTOR_OUT1: U4.6 (OUT1); also elsewhere on the board
MOTOR_OUT2: U4.8 (OUT2); also elsewhere on the board
unnamed: D2.2 (A), R13.2
unnamed: R12.1, U4.4 (ILIM)
UI_3V3: R13.1; also elsewhere on the board
UI_KEY0: SW1.2; also elsewhere on the board
UI_KEY1: SW2.2; also elsewhere on the board
UI_LED: D2.1 (K); also elsewhere on the board
VBAT: C15.1, C16.1, U4.5 (VM); also elsewhere on the board

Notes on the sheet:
UI:
Misc.:
On UI sub-PCB
Magnet sensors:
Motor driver:
On door sensor sub-PCB

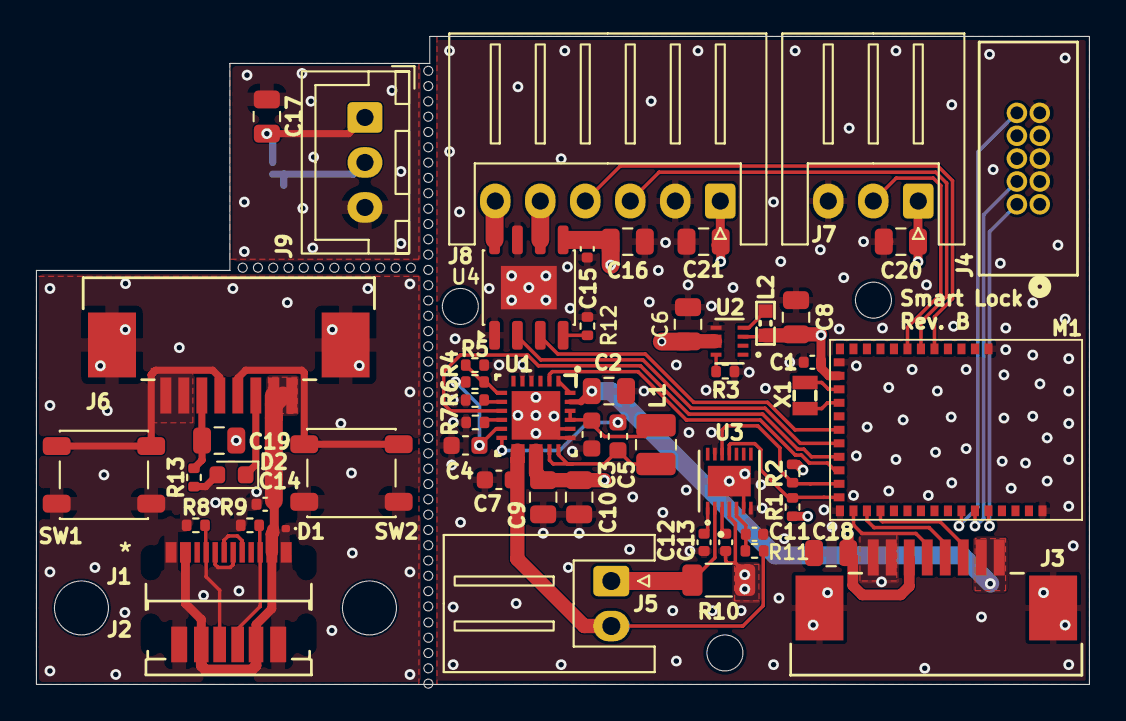
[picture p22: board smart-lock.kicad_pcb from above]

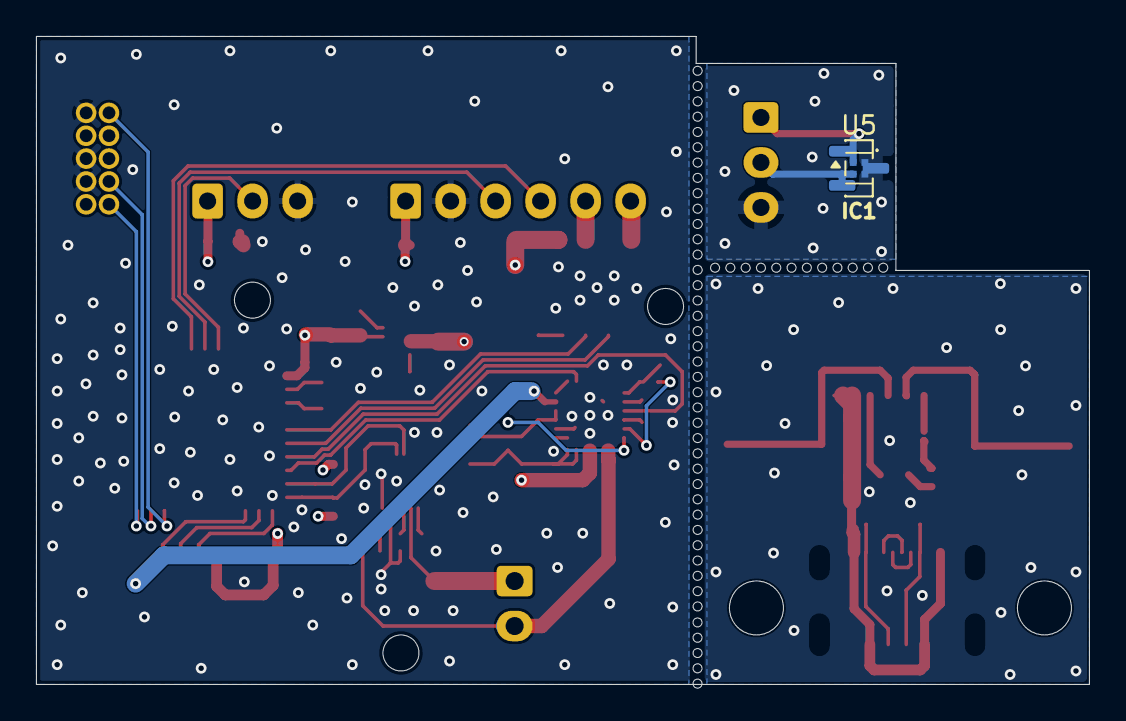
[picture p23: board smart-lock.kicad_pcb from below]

Board: 4 copper layers, 58.5 x 36.0 mm, 57 parts (2 on the bottom side), 53 nets.

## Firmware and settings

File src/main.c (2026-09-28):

#include <zephyr/kernel.h>
#include <zephyr/logging/log.h>
#include <zephyr/sys/reboot.h>

#include <ram_pwrdn.h>

#include "radio.h"
#include "lock_manager.h"
#include "door_monitor.h"
#include "battery_manager.h"
#include "watchdog.h"
#include "ui.h"

LOG_MODULE_REGISTER(app, CONFIG_LOG_DEFAULT_LEVEL);

/* --- Lock state changed — application-level handler ----------------- */

static void on_lock_state_changed(const struct lock_state_change *change)
{
	radio_on_lock_state_changed(change);

	/*
	 * Poll the gauge once the bolt is at rest, while the motor load is still
	 * reflected in the readings. UNLATCHED is skipped because its settle to
	 * UNLOCKED follows within seconds and would poll again for nothing.
	 */
	if (change->state == LOCK_STATE_LOCKED ||
	    change->state == LOCK_STATE_UNLOCKED) {
		battery_manager_poll();
	}
}

/* --- UI callbacks --------------------------------------------------- */

/*
 * No originator: a key press has no client behind it, and MANUAL is what a
 * Matter controller turns into "unlocked at the door" rather than attributing
 * the action to a fabric member.
 */
static int on_ui_lock_request(enum lock_action action)
{
	return lock_manager_request(action, LOCK_OP_SOURCE_MANUAL, NULL);
}

static const struct ui_cb ui_cbs = {
	.lock_request = on_ui_lock_request,
	.start_discovery = radio_start_discovery,
	.factory_reset = radio_factory_reset,
};

/* --- Battery callbacks ----------------------------------------------- */

static void on_charger_changed(bool charging, bool complete)
{
	ui_on_charging_changed(charging, complete);
	radio_on_charger_changed(charging, complete);
}

static const struct battery_manager_cb battery_cbs = {
	.on_battery_changed = radio_on_battery_changed,
	.on_charger_changed = on_charger_changed,
};

/* --- Radio callbacks ------------------------------------------------ */

static const struct radio_cb radio_cbs = {
	.lock_request = lock_manager_request,
	.on_discovery_changed = ui_on_discovery_changed,
	.on_identify = ui_on_identify,
};

/* --- Main ----------------------------------------------------------- */

int main(void)
{
	int err;

	/*
	 * Power down the SRAM sections above the image. Called here rather than
	 * left to the library's own SYS_INIT, which only exists under
	 * CONFIG_RAM_POWER_ADJUST_ON_HEAP_RESIZE — that needs newlib, and Matter
	 * forces picolibc, so nothing would call it in a BLE-only build.
	 */
	power_down_unused_ram();

	/*
	 * Peripheral init failures are logged but not fatal: the hardware may
	 * simply not be connected during development, and the radio is still
	 * worth bringing up.
	 *
	 * These register callbacks that lead into the radio layer, and the
	 * sensor interrupts are live from here, so radio.c ignores anything
	 * arriving before radio_init() rather than dispatching into backends
	 * that do not exist yet.
	 */
	err = lock_manager_init(on_lock_state_changed);
	if (err) {
		LOG_WRN("App: lock manager init failed (hardware absent?): %d",
			err);
	}

	err = door_monitor_init(radio_on_door_state_changed);
	if (err) {
		LOG_WRN("App: door monitor init failed (hardware absent?): %d",
			err);
	}

	err = ui_init(&ui_cbs);
	if (err) {
		LOG_WRN("App: UI init failed (hardware absent?): %d", err);
	}

	err = battery_manager_init(&battery_cbs);
	if (err) {
		LOG_WRN("App: battery init failed (hardware absent?): %d", err);
	}

	/* Before the radio, which claims a watchdog channel of its own. */
	err = watchdog_init();
	if (err) {
		LOG_ERR("App: watchdog init failed: %d", err);
		return err;
	}

	err = radio_init(&radio_cbs);
	if (err) {
		/*
		 * Reboot rather than return: the watchdog is already being fed
		 * from the system workqueue, so a bare return would leave a
		 * radio-less lock sitting there looking healthy.
		 */
		LOG_ERR("App: radio init failed, rebooting: %d", err);
		sys_reboot(SYS_REBOOT_WARM);
	}

	/*
	 * Publish the state the hardware was found in, now that the backends
	 * exist. operated stays clear: nobody operated the lock, and a Matter
	 * build would otherwise announce an operation on every boot.
	 *
	 * The door is deliberately absent. Its only non-eventing publish path
	 * runs from the Matter cluster init callback inside radio_init() (see
	 * matter_radio_publish_initial_state), whereas going through
	 * radio_on_door_state_changed() here would reach SetDoorState() and emit
	 * a DoorStateChange event as if the door had just moved. BLE needs no
	 * seeding — it has no subscribers yet and serves reads on demand.
	 */
	struct lock_state_change initial_state = {
		.state = lock_manager_get_state(),
		.source = LOCK_OP_SOURCE_MANUAL,
	};

	radio_on_lock_state_changed(&initial_state);
	radio_on_battery_changed(battery_get_soc(), battery_get_voltage(),
				 battery_get_remaining_mah());
	radio_on_charger_changed(battery_is_charging(),
				 battery_is_charge_complete());

	LOG_INF("App: ready (version %s)", APP_VERSION_STRING);

	return radio_run();
}

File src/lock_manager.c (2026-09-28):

#include "lock_manager.h"
#include "gpio_input.h"

#include <string.h>

#include <zephyr/kernel.h>
#include <zephyr/init.h>
#include <zephyr/drivers/gpio.h>
#include <zephyr/logging/log.h>

LOG_MODULE_REGISTER(lock_manager, CONFIG_LOG_DEFAULT_LEVEL);

/* Motor driver GPIOs */
#define MOTOR_NODE DT_NODELABEL(motor_driver)

/*
 * nSLEEP is optional (rev A DRV8837 has it, rev B DRV8871 does not). When
 * absent GPIO_DT_SPEC_GET_OR yields a NULL port, so every access is guarded.
 */
static const struct gpio_dt_spec motor_nsleep =
	GPIO_DT_SPEC_GET_OR(MOTOR_NODE, nsleep_gpios, {0});
static const struct gpio_dt_spec motor_in1 =
	GPIO_DT_SPEC_GET(MOTOR_NODE, in1_gpios);
static const struct gpio_dt_spec motor_in2 =
	GPIO_DT_SPEC_GET(MOTOR_NODE, in2_gpios);

/* Hall-effect position sensors (gpio-keys compatible) */
static const struct gpio_dt_spec lock_sensor_gpio =
	GPIO_DT_SPEC_GET(DT_ALIAS(lock_sensor), gpios);
static const struct gpio_dt_spec unlock_sensor_gpio =
	GPIO_DT_SPEC_GET(DT_ALIAS(unlock_sensor), gpios);

/*
 * lock_manager_request() is called from the BLE and Matter threads while the
 * state is modified from the system workqueue, so the mutex serializes access.
 *
 * State changes are staged here and delivered by unlock_and_notify() once the
 * mutex is released, never from inside it. state_cb reaches bt_gatt_notify(),
 * which waits K_FOREVER for an ATT buffer on any thread that is not the system
 * workqueue (see the timeout selection in Zephyr's att.c). Called under the
 * mutex, the BT RX thread would hold it while waiting for buffers that only the
 * system workqueue recycles — and the system workqueue would be blocked on the
 * same mutex.
 */
static K_MUTEX_DEFINE(lock_mutex);

/* Deepest run is a set_state() plus the settle in finish_operation(). */
static struct lock_state_change pending[3];
static uint8_t pending_count;

static enum lock_state current_state;
static lock_state_changed_cb_t state_cb;
static bool motor_running;
static enum lock_action motor_action;
static enum lock_op_source motor_source;
static struct lock_originator motor_originator;

static const char *lock_state_str(enum lock_state state)
{
	switch (state) {
	case LOCK_STATE_LOCKED: return "locked";
	case LOCK_STATE_LOCKING: return "locking";
	case LOCK_STATE_UNLOCKED: return "unlocked";
	case LOCK_STATE_UNLOCKING: return "unlocking";
	case LOCK_STATE_JAMMED: return "jammed";
	case LOCK_STATE_UNKNOWN: return "unknown";
	case LOCK_STATE_UNLATCHED: return "unlatched";
	}
	return "?";
}

static struct k_work motor_timeout_work;
static struct k_work motor_complete_work;

static struct k_timer motor_timeout_timer;
static struct k_timer motor_complete_timer;

static struct gpio_input lock_sensor_input;
static struct gpio_input unlock_sensor_input;

/*
 * Sequence number of the operation currently owning the motor, and the sequence
 * each timed phase was armed for.
 *
 * k_timer_stop() keeps a stopped timer from expiring again, but it cannot
 * unqueue work that an earlier expiry already submitted, and a handler that has
 * begun running is merely blocked on the mutex. So a phase handler can reach the
 * critical section belonging to an operation that has since been replaced —
 * where motor_running is true again and every other check passes. It would then
 * brake a motor run it knows nothing about, or declare it jammed.
 *
 * Each phase therefore records which operation armed it and verifies that
 * operation is still the current one. Comparison is by equality only, so the
 * counter wrapping is harmless.
 *
 * complete_armed tracks the same thing within one operation, which the sequence
 * numbers cannot: k_timer_remaining_get() reads 0 both for a stopped timer and
 * for one that has expired but whose work has not run yet, so using it as the
 * armed flag would let a sensor edge re-arm the phase under the already-queued
 * handler and stop the motor early.
 */
static uint32_t operation_seq;
static uint32_t timeout_seq;
static uint32_t complete_seq;
static bool complete_armed;

static void arm_timeout(uint32_t delay_ms)
{
	timeout_seq = operation_seq;
	k_timer_start(&motor_timeout_timer, K_MSEC(delay_ms), K_NO_WAIT);
}

static void arm_complete(uint32_t delay_ms)
{
	complete_seq = operation_seq;
	complete_armed = true;
	k_timer_start(&motor_complete_timer, K_MSEC(delay_ms), K_NO_WAIT);
}

/* Stage a state change for delivery after the mutex is dropped. */
static void notify_state(enum lock_state new_state, enum lock_op_source source,
			 bool operated)
{
	if (current_state == new_state) {
		return;
	}

	LOG_INF("Lock: %s -> %s", lock_state_str(current_state),
		lock_state_str(new_state));
	current_state = new_state;

	if (!state_cb) {
		return;
	}

	if (pending_count >= ARRAY_SIZE(pending)) {
		LOG_ERR("Lock: dropped %s notification", lock_state_str(new_state));
		return;
	}

	struct lock_state_change *change = &pending[pending_count++];

	*change = (struct lock_state_change){
		.state = new_state,
		.source = source,
		.operated = operated,
	};

	/* Only a remote operation has a client identity worth reporting. */
	if (operated && source == LOCK_OP_SOURCE_REMOTE) {
		change->originator = motor_originator;
	}
}

static void unlock_and_notify(void)
{
	struct lock_state_change flush[ARRAY_SIZE(pending)];
	uint8_t count = pending_count;

	memcpy(flush, pending, count * sizeof(flush[0]));
	pending_count = 0;

	k_mutex_unlock(&lock_mutex);

	for (uint8_t i = 0; i < count; i++) {
		state_cb(&flush[i]);
	}
}

/* A position reached because someone asked for it. */
static void set_state(enum lock_state new_state, enum lock_op_source source)
{
	notify_state(new_state, source, true);
}

/*
 * A position the mechanism reached on its own, with nobody operating the lock —
 * currently only the spring latch re-engaging after an open. The source of the
 * operation that led here is carried through for context, but consumers are
 * told not to log this as an operation.
 */
static void settle_state(enum lock_state new_state)
{
	notify_state(new_state, motor_source, false);
}

static void motor_stop(void)
{
	gpio_pin_set_dt(&motor_in1, 0);
	gpio_pin_set_dt(&motor_in2, 0);
	if (motor_nsleep.port) {
		gpio_pin_set_dt(&motor_nsleep, 0);
	}
	motor_running = false;
	complete_armed = false;
	k_timer_stop(&motor_timeout_timer);
	k_timer_stop(&motor_complete_timer);
}

static void motor_brake(uint32_t usec)
{
	gpio_pin_set_dt(&motor_in1, 1);
	gpio_pin_set_dt(&motor_in2, 1);
	k_busy_wait(usec);
	gpio_pin_set_dt(&motor_in1, 0);
	gpio_pin_set_dt(&motor_in2, 0);
}
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
